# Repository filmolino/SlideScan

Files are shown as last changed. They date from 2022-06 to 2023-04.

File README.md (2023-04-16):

# SlideScan

**Note:** There is a new version of the slide scanner using a M5Stack Fire for more info visit [Filmolino SlideScanner](https://github.com/filmolino/SlideScanner)

Filmolino SlideScan is a device that makes it easy to scan slides in magazines fully automatic using a modified slide projector and a digital camera. It controls the slide projector and a digital camera using a cable release or an infrared remote control (Nikon, Canon, Pentax, Sony, Olympus, Minolta). It is powered directly from the slide projector or over a mini USB connector. New cable releases and IR controls can easy be added to the software. 
 
Thanks to the [M5StampC3 from M5Stack](https://shop.m5stack.com/collections/m5-controllers/products/m5stamp-c3-mate-with-pin-headers) using a [ESP32-C3 RISC-V microcontroller from Espressif](https://www.espressif.com/en/products/socs/esp32-c3) it is also possible to control the SlideScan through a web interface over WiFi. The scanner has it's own access point to which you can connect.

Everything of the SlideScan is open source, so you can easy build your own!

## Guide
### Camera connection
You can connect your digital camera using a cable connection or infrared remote control. To control your camera using the cable release you need a shutter release cable for your camera with a 2.5 mm jack connector on the other end. You can find the right cable for your camera searching the web for *JJC Remote Control Shutter Release Cable*. They are not expensive you should get one for about 10 EUR.

### DIN cable connection to pcb
Connect the male 6 pin DIN connector as follows to the PCB J2:

| Pin DIN | Pin PCB |Function |
| --- | --- | --- |
| 1 | 4 | Reverse slide transport |
| 2 | 3 | Forward slide transport |
| 3 | 2 | Positive DC voltage |
| 4 | x | Not used |
| 5 | x | Not used |
| 6 | 1 | Negative DC voltage (only needed if you want to power SlideScan from the projector) |

### Slide projector connection
**Important: Use the Tape/remote control socket and not the lap dissolve socket.**
Connect the 6 pin DIN connector of the Filmolino SlideScan to the *remote control socket* of your slide projector. SlideScan can be powered from the slide projector or you can power it over the Mini USB connector. 

To power it from the projector the following components *R2, C4, U1, C3, D2* need to be assembled on the pcb. If you power SlideScan over USB you don't need this components.

To not damage your SlideScan or slide projector check the pin map below first!
| 6 pin DIN connector | Function |
| --- | --- |
| 1 | Reverse slide transport |
| 2 | Forward slide transport |
| 3 | Positive DC voltage **max. 42 VDC!** (This voltage is usually about 30...35 VDC on most slide projectors) |
| 4 | Focus motor |
| 5 | Not used |
| 6 | Negative DC voltage |

### USB power
If you don't want to power your SlideScan from the slide projector connect an USB charger to the mini USB connector of the SlideScan.

### Turn on
Now you are ready to turn SlideScan on. To do so turn on the slide projector and if needed the USB charger.
After turning on the green LED should light up and the red one slowly blinking (because there is no WiFi connection yet).

### WiFi Connection
SlideScan starts its own WiFi access point: 

Default WiFi credentials
| ID | value |
| --- | --- |
| SSID | scanner |
| Password | filmolino |
| IP | 192.168.4.1 |

To see the web user interface do the following:
1. Connect your PC/Tablet/... to the SlideScan network with the SSID **scanner** using the password **filmolino**
2. In your webbrowser enter the address: **192.168.4.1**
3. Now you should see the web interface of the scanner

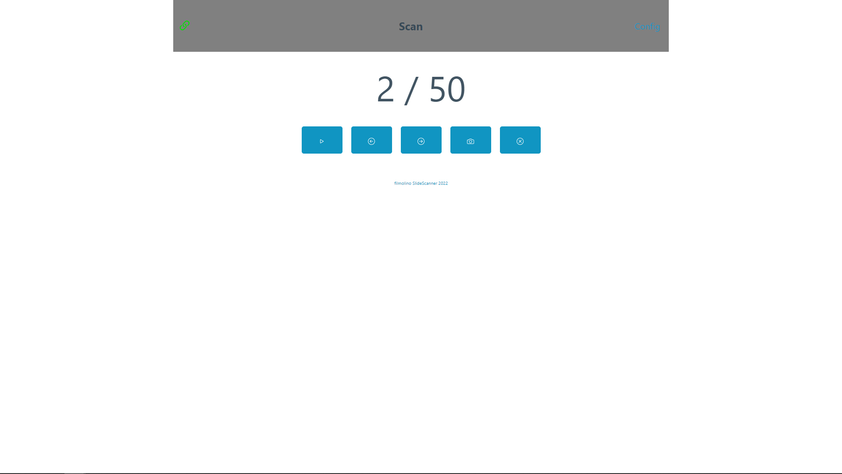
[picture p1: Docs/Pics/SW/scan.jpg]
Scanner Web interface scan dialog


### Configuration
To see the configuration menu click on **Config**.

#### Access Point
Here you can change the SSID and the password.

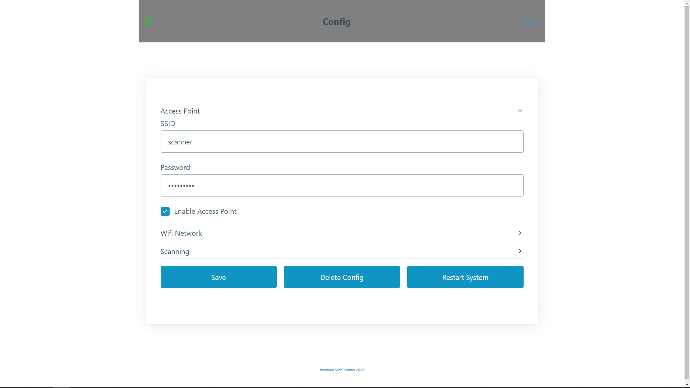
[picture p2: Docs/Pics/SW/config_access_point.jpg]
Config access point


#### WiFi Network
Not implemented yet.

#### Scanning
Here you can config the SlideScan.

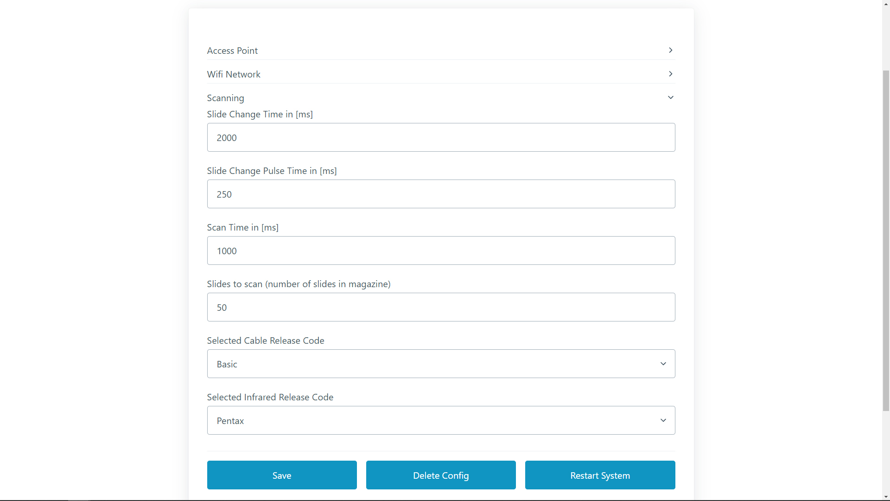
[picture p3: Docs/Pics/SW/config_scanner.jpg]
Config scanner


##### Slide Change Time
This is the time the slide projector needs to change the slide.
Unit is milliseconds (1 second = 1000 milliseconds)

##### Slide Change Pulse Time
Duration of the pulse for the slide transport. During this time the slide transport contacts are closed. 
Unit is milliseconds (1 second = 1000 milliseconds)

##### Scan Time
This is the time the digital camera needs to capture (scan) the slide
Unit is milliseconds (1 second = 1000 milliseconds)

##### Slides to scan
Number of slides in the magazine.

##### Selected cable release
Can be OFF or the cable release you want to use.

##### Selected Infrared Release Code
Can be OFF or the brand name of your digital camera.

##### Buttons
| Button | Function |
| --- | --- |
| Save | Saves the changes |
| Delete Config | Deletes the actual configuration, you need to click the *Restart System* button after that |
| Restart System | Restarts the scanner |

### Standalone operation 
The device is controlled with only two buttons. The functions are as follows:

| Button | Short press | Long press |
| --- | --- | --- |
| Left | Forward slide transport | Backward slide transport |
| Right | Trigger camera (if auto an auto scan is active, stop it) | Start auto scan |

The actual state is indicated by a bi-color LED:
| State | LED green | LED red |
| --- | --- | --- |
| Running and no WiFi connection | ON | BLINK slowly |
| Running with WiFi connection | ON | OFF |
| Auto scan active | BLINK | OFF |
| Error | OFF | ON |

#### Auto Scan
When starting an Auto Scan the scan is always starts with image 1 and then the number of images is scanned. If the image counter is higher it will be reset to 1 before start.

### WiFi operation
Connect to the WiFi and open the address **192.168.4.1** in your webbrowser as described above. The SlideScan is connected as long as you see the green connected sign in the top left corner.

This view shows the current slide counter and the slides in the magazine (0/50). 
You can start an auto scan or manually scan slides using the five buttons below. If you want to change the current configuration click *Config* in the top right corner.

Buttons
| Button 1 | Button 2 | Button 3 | Button 4 | Button 5 |
| --- | --- | --- | --- | --- |
| Start Auto Scan | Forward | Backward | Capture (Scan) | Reset current slide |

To change to number of slides in the current magazine you can click on the current slide counter or go to the config menu.

## Hardware
You can find the KiCAD project with complete schematic and pcb design in the hardware folder. The double sided pcb can be easily soldered by hand. It uses just a few SMD components in not too small cases (0805). The components are easily available from the usual distributors.

## Software
### Project
The software is build with ESP-IDF using platform.io and Visual Studio Code.

## Documentation
The documentation with images can be found in the docs folder.

## To do
- slidescan.local address not working yet. So you have to point your browser to the default IP **192.168.4.1**
- Station mode (to connect to a WiFi network) not working yet
- Tested with Nikon and Pentax cameras

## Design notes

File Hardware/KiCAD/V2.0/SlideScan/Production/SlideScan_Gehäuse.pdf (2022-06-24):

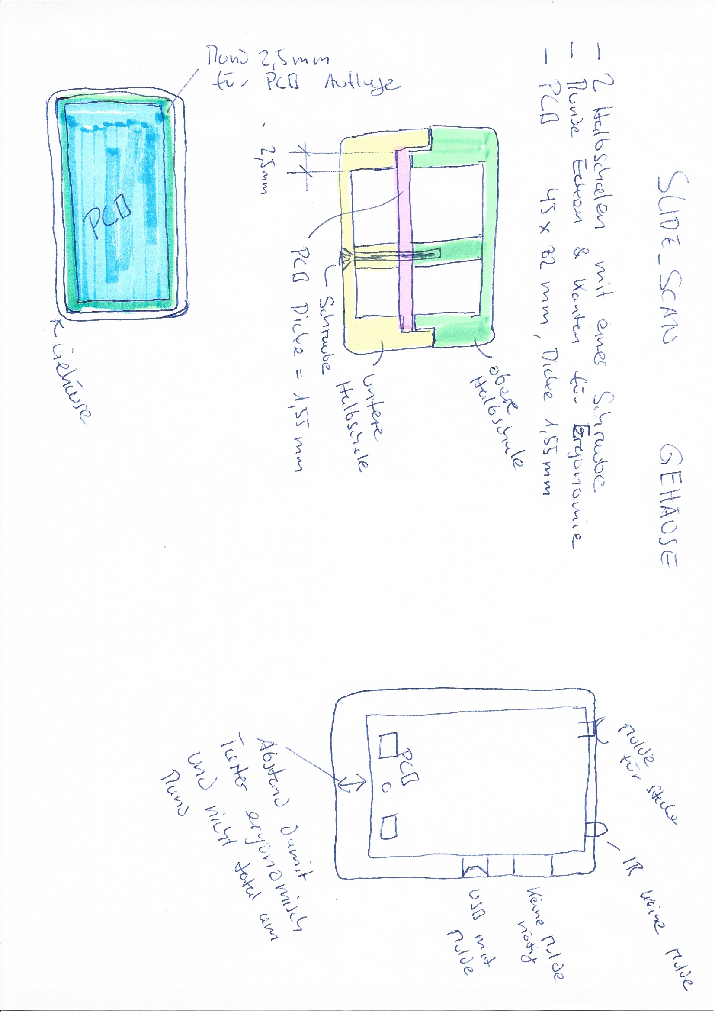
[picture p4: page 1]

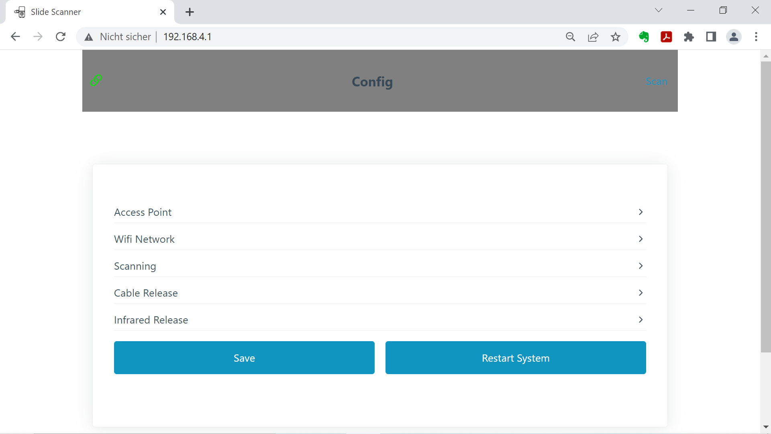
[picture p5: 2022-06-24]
Docs/Pics/Prototype/Screenshot (2).png

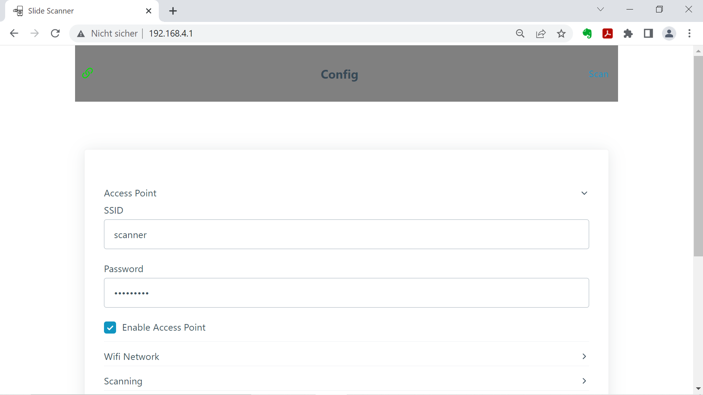
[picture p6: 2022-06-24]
Docs/Pics/Prototype/Screenshot (4).png

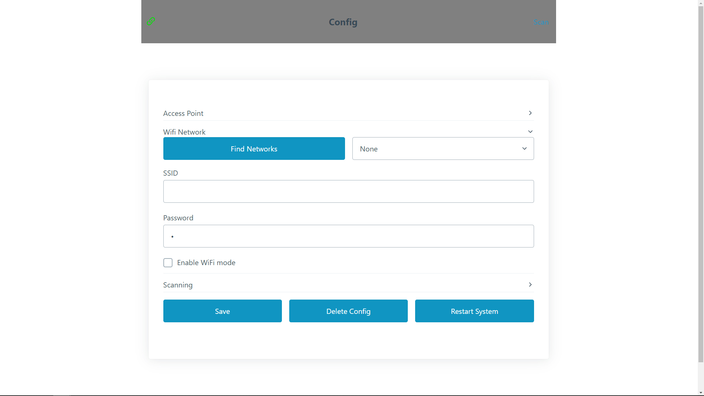
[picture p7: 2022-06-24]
Docs/Pics/SW/config_wifi.jpg

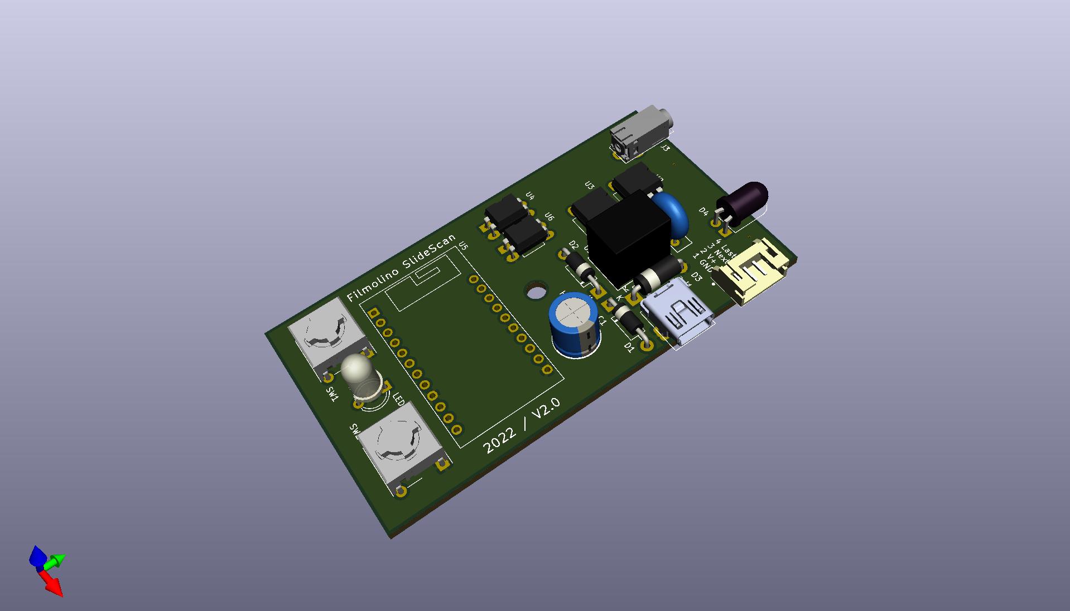
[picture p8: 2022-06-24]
Docs/Pics/HW/V2.0/SlideScan_TopView_KiCAD.jpg

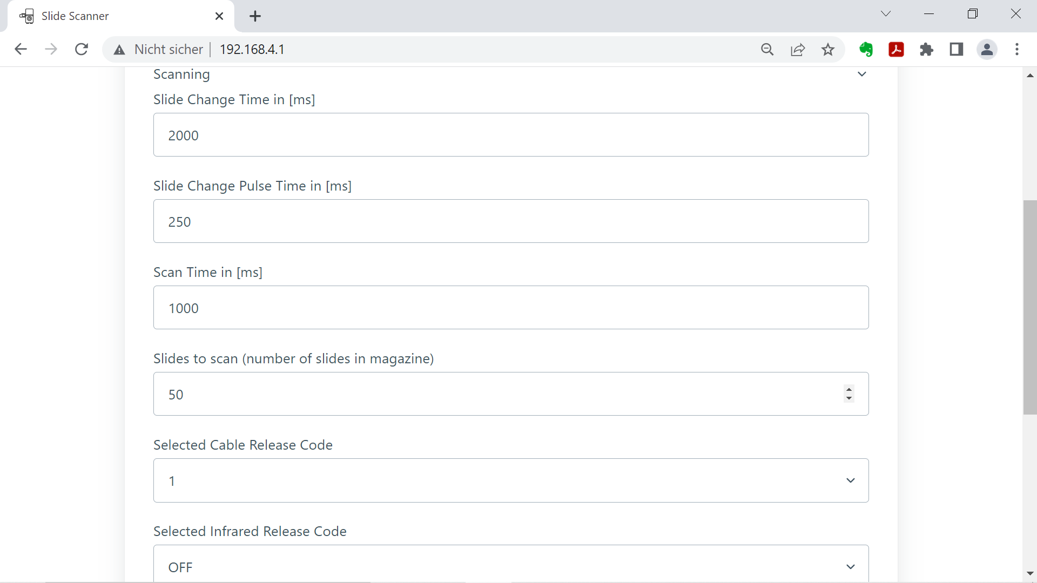
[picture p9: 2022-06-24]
Docs/Pics/Prototype/Screenshot (3).png

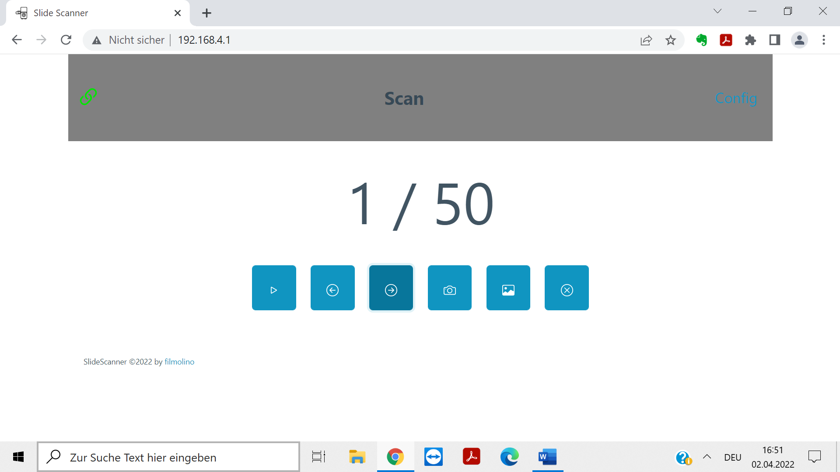
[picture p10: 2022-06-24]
Docs/Pics/Prototype/Screenshot (1).png

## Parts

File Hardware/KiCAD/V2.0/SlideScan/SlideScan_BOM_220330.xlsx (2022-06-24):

Ref | Qnty | Value | Cmp name | Footprint | Lieferant | Einzelpreis [EUR] | Preis [EUR]
C1, | 1 | 470uF/10V | CP | Capacitor_THT:CP_Radial_D8.0mm_P3.50mm | Reichelt | 0.4 | 0.4
C2, C5, | 2 | 100nF/50V/MLCC | C | Capacitor_SMD:C_0805_2012Metric_Pad1.15x1.40mm_HandSolder | Reichelt | 0.1 | 0.2
C3, C6, | 2 | 10uF/10V/MLCC | C | Capacitor_SMD:C_0805_2012Metric_Pad1.15x1.40mm_HandSolder | Distrelec | 0.4 | 0.8
C4, | 1 | 10uF/100V/MLCC | C | Capacitor_SMD:C_1210_3225Metric_Pad1.42x2.65mm_HandSolder | Distrelec | 0.7 | 0.7
D1, D2, | 2 | 1N5817 | 1N5817 | Diode_THT:D_DO-41_SOD81_P10.16mm_Horizontal | Reichelt | 0.1 | 0.2
D3, | 1 | BZW06-5V8 | 1N62xxA | Diode_THT:D_DO-15_P10.16mm_Horizontal | Reichelt | 0.3 | 0.3
D4, | 1 | LD 274 | LED | LED_THT:LED_D5.0mm_Horizontal_O1.27mm_Z3.0mm_IRBlack | Reichelt | 1.1 | 1.1
F1, | 1 | FRX03060F | Polyfuse | Varistor:RV_Disc_D9mm_W3.3mm_P5mm | Reichelt | 0.4 | 0.4
J1, | 1 | USB_B_Mini RND 205-00862 | USB_B_Mini | SlideScan:USB_Mini_RND_205-00862 | Distrelec | 1.35 | 1.35
J2, | 1 | Conn_01x04 | Conn_01x04 | Connector_PinSocket_2.54mm:PinSocket_1x04_P2.54mm_Vertical | Einlöten | 0 | 0
J3, | 1 | Lumberg 1501 04 | AudioJack3 | SlideScan:Jack_2.5mm_Lumberg_1501_04 | Reichelt | 1.2 | 1.2
L1, | 1 | L | L | Inductor_SMD:L_0805_2012Metric_Pad1.15x1.40mm_HandSolder | Reichelt | 0.3 | 0.3
LED1, | 1 | Everlight 339-1SDRSYGW/S530-A3/S150 | LED_Dual_ACA | SlideScan:LED_D5.0mm-3_Everlight | Reichelt | 0.2 | 0.2
Q1, | 1 | BSS138 | BSS138 | Package_TO_SOT_SMD:SOT-23 | Reichelt | 0.2 | 0.2
R1, R2, R3, R4, R8, R9, R10, | 7 | 180R | R | Resistor_SMD:R_0805_2012Metric_Pad1.15x1.40mm_HandSolder | Reichelt | 0.05 | 0.35
R5, | 1 | R | R | Resistor_SMD:R_0805_2012Metric_Pad1.15x1.40mm_HandSolder | Reichelt | 0.05 | 0.05
R6, | 1 | 10k | R | Resistor_SMD:R_0805_2012Metric_Pad1.15x1.40mm_HandSolder | Reichelt | 0.05 | 0.05
R7, | 1 | 1M | R | Resistor_SMD:R_0805_2012Metric_Pad1.15x1.40mm_HandSolder | Reichelt | 0.05 | 0.05
R11, | 1 | 0R | R | Resistor_SMD:R_0805_2012Metric_Pad1.15x1.40mm_HandSolder | Reichelt | 0.05 | 0.05
SW1, SW2, | 2 | MEC APEM 5ETH935 | SW_Push | SlideScan:SW_MEC_5ETH9 | Reichelt | 1.35 | 2.7
U1, | 1 | R78C5.0-1.0 | R78C5.0-1.0 | SlideScan:RECOM_SIP3_R-78C5.0-1.0 | Reichelt | 11.5 | 11.5
U2, U3, U4, U6, | 4 | VO14642AT | VO14642AT | Package_DIP:DIP-6_W7.62mm | Distrelec | 3.2 | 12.8
U5, | 1 | M5StampC3_C3U | M5StampC3_C3U | SlideScan:M5StampC3 | Distrelec | 7.1 | 7.1 | C3U Version
Gehäuse | 1 | Hammond MFG 1591XXABK |  |  | Reichelt | 3.75 | 3.75
Tasterkappen | 2 | Apem MEC 12 mm 1SS09-12.0 |  |  | Reichelt | 0.25 | 0.5
PCB | 1 | PCB |  |  | MultiCircuitBoards | 7.5 | 7.5
 |  |  |  |  |  | TOTAL | 53.75
 |  |  |  |  |  | Ohne PCB | 46.25
 |  |  |  |  |  | Ohne Dia Power | 41.15

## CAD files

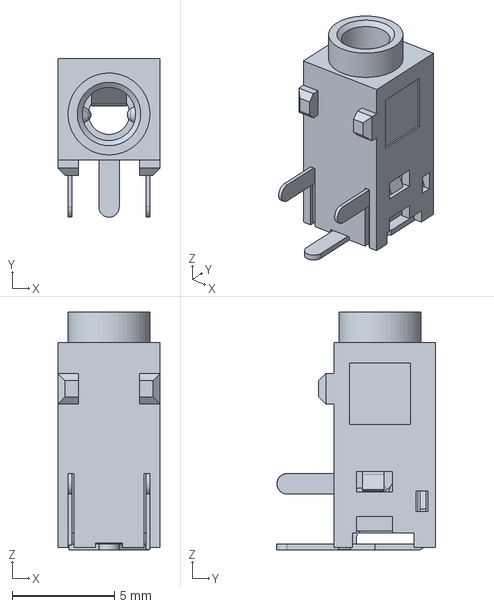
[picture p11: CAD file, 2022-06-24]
Hardware/Footprints/3d/lumberg_1501_04.stp
5.00 x 7.75 x 11.6 mm

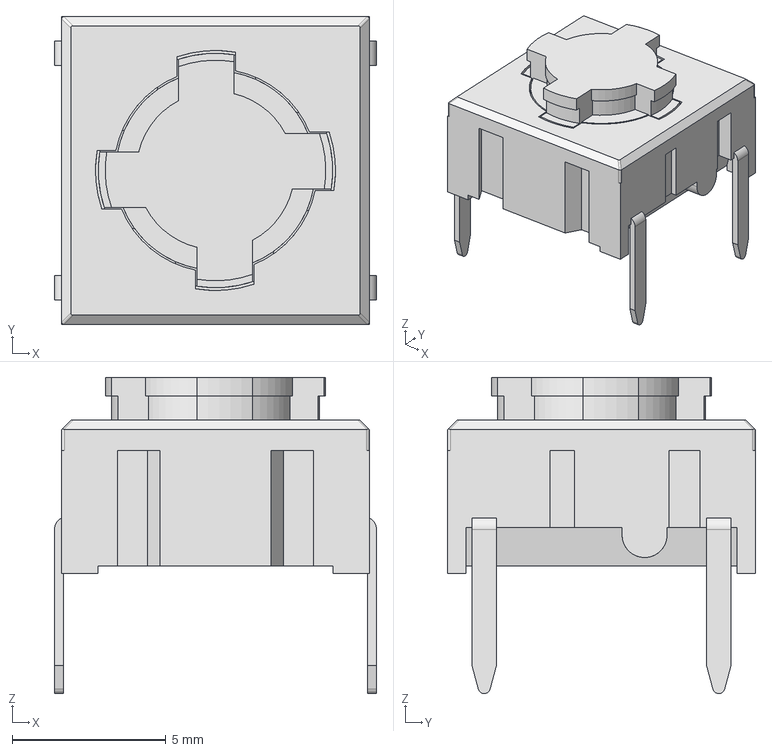
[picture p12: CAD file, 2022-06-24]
Hardware/Footprints/3d/5ETH9XX.stp
10.5 x 10.0 x 10.3 mm

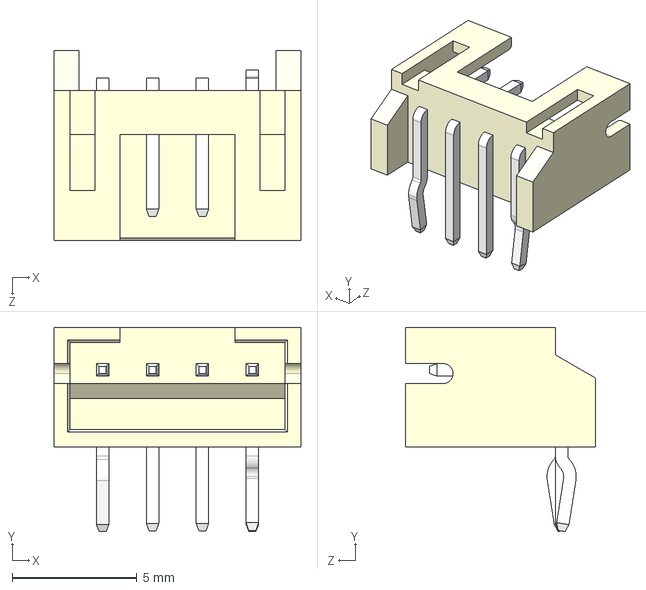
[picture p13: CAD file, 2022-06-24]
Hardware/Footprints/3d/S4B-PH-K-S(LF)(SN)--3DModel-STEP-56544.STEP
9.90 x 8.18 x 7.60 mm

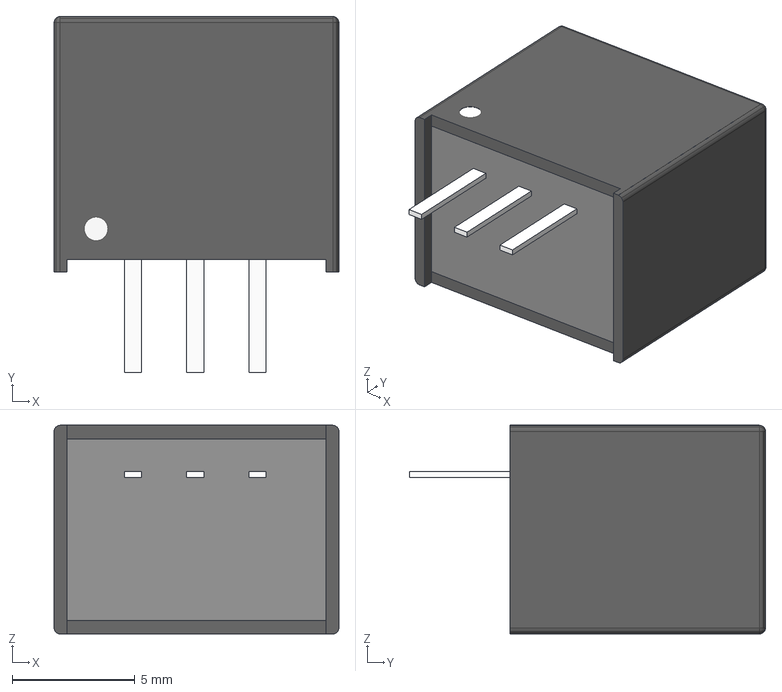
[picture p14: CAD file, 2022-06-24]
Hardware/Footprints/3d/R-78C5.0-1.0--3DModel-STEP-1.STEP
11.6 x 14.5 x 8.51 mm

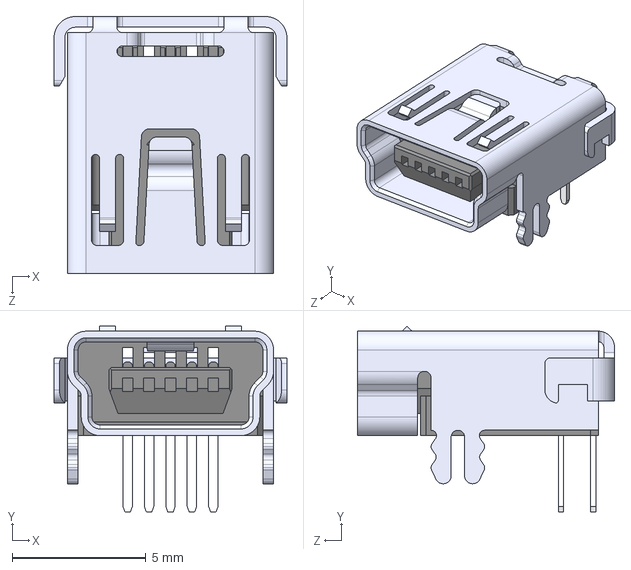
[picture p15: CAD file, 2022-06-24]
Hardware/Footprints/3d/2172034-1--3DModel-STEP-56544.STEP
8.70 x 6.94 x 9.60 mm

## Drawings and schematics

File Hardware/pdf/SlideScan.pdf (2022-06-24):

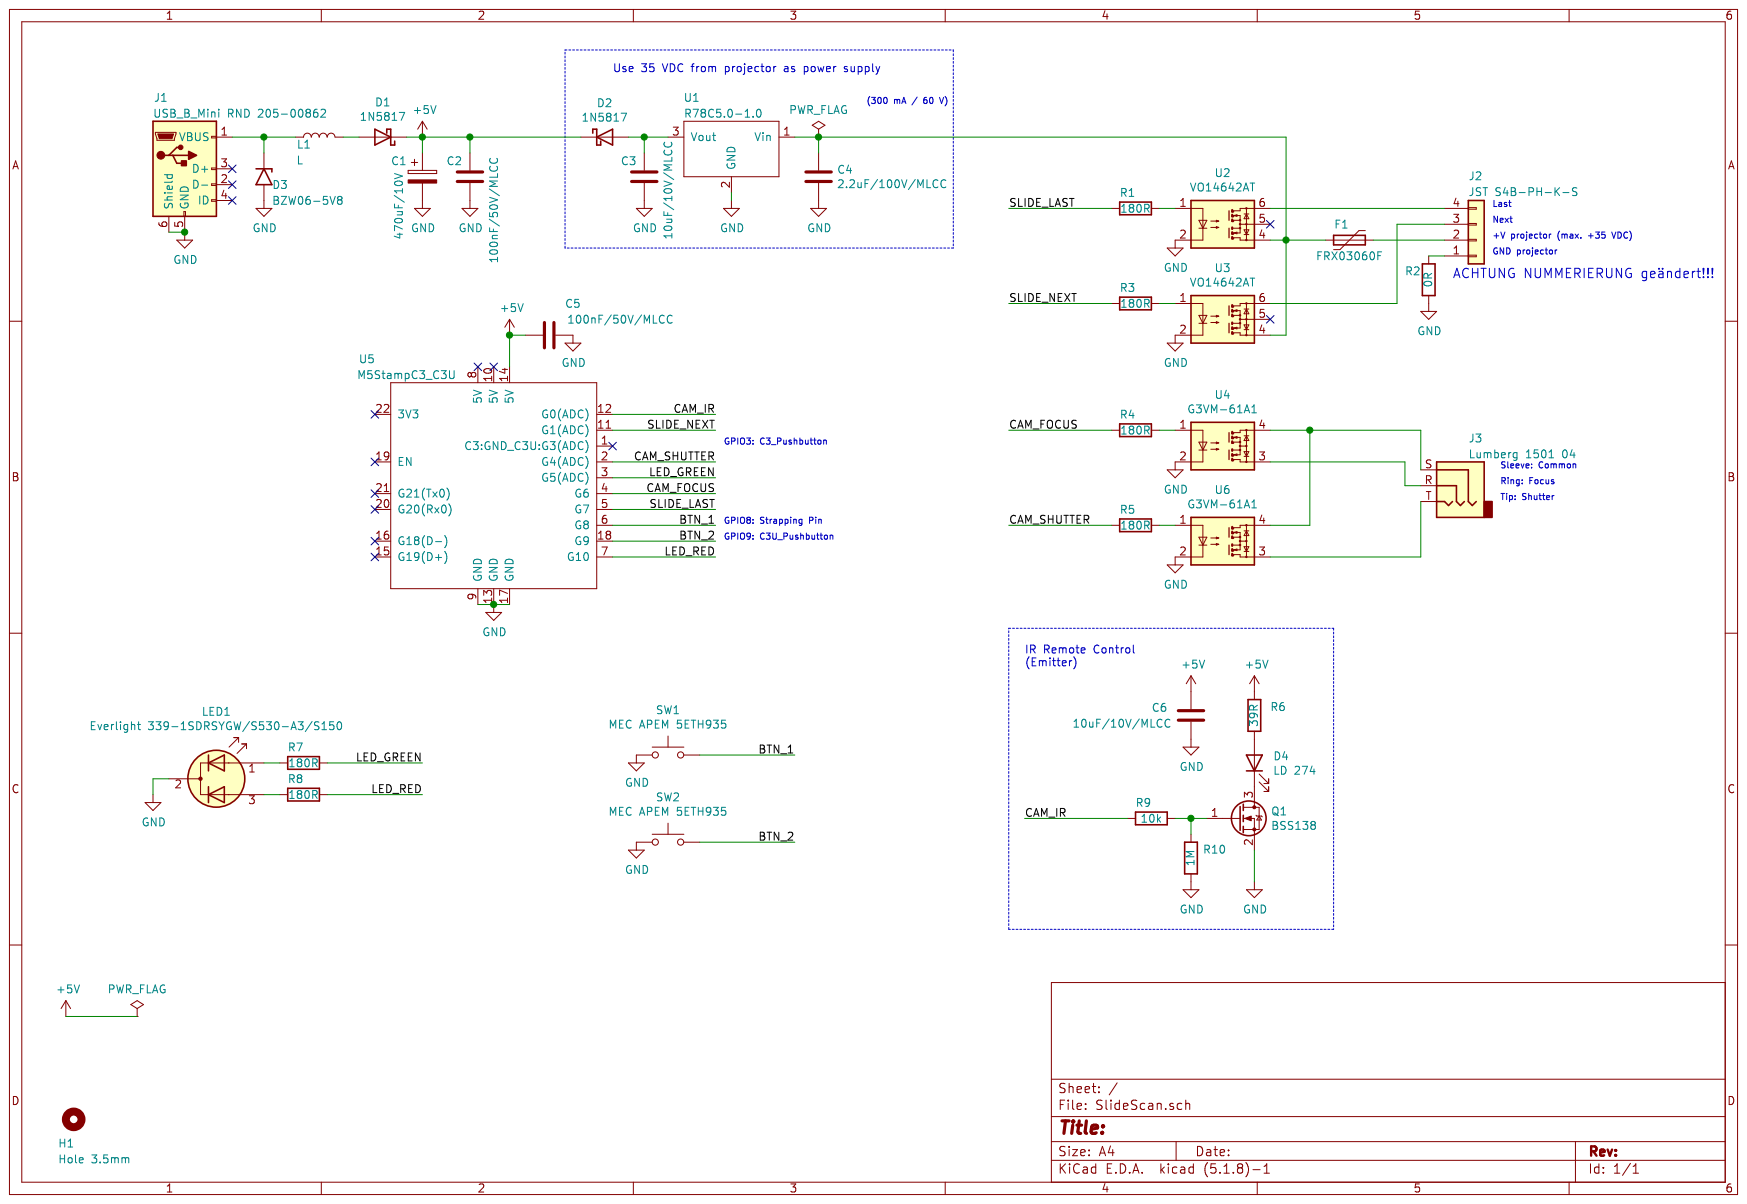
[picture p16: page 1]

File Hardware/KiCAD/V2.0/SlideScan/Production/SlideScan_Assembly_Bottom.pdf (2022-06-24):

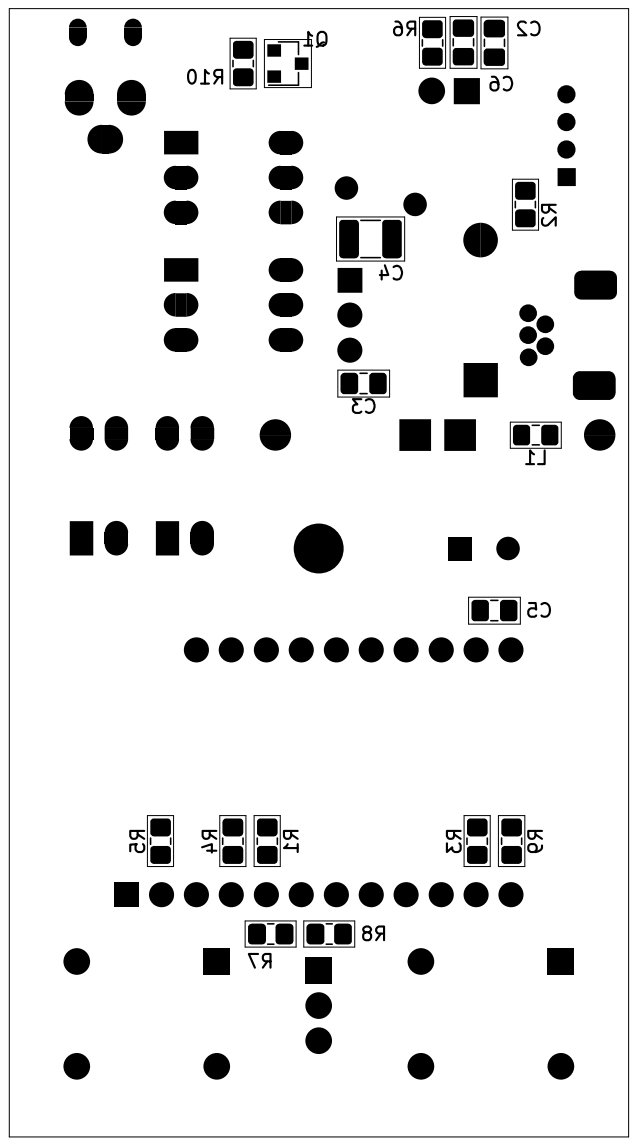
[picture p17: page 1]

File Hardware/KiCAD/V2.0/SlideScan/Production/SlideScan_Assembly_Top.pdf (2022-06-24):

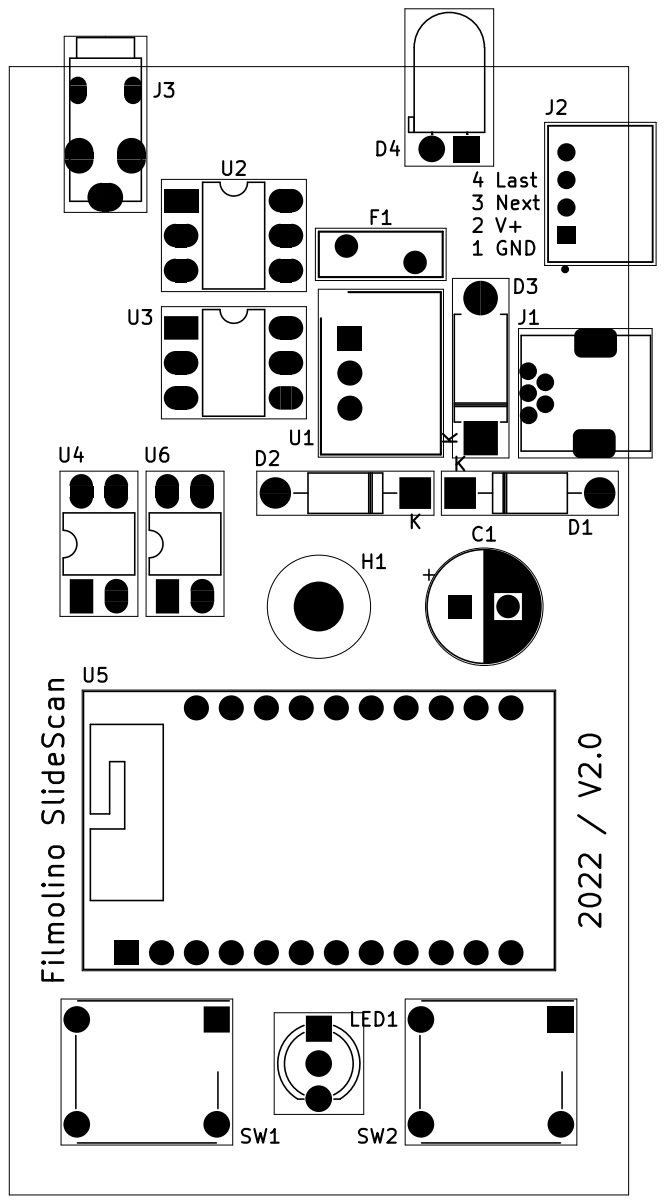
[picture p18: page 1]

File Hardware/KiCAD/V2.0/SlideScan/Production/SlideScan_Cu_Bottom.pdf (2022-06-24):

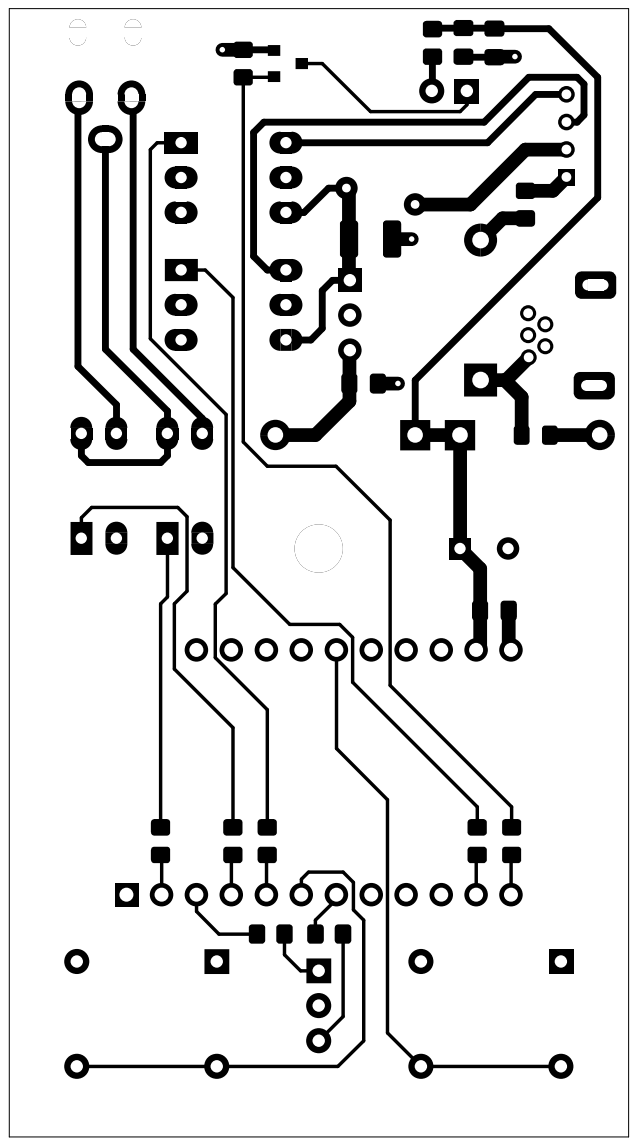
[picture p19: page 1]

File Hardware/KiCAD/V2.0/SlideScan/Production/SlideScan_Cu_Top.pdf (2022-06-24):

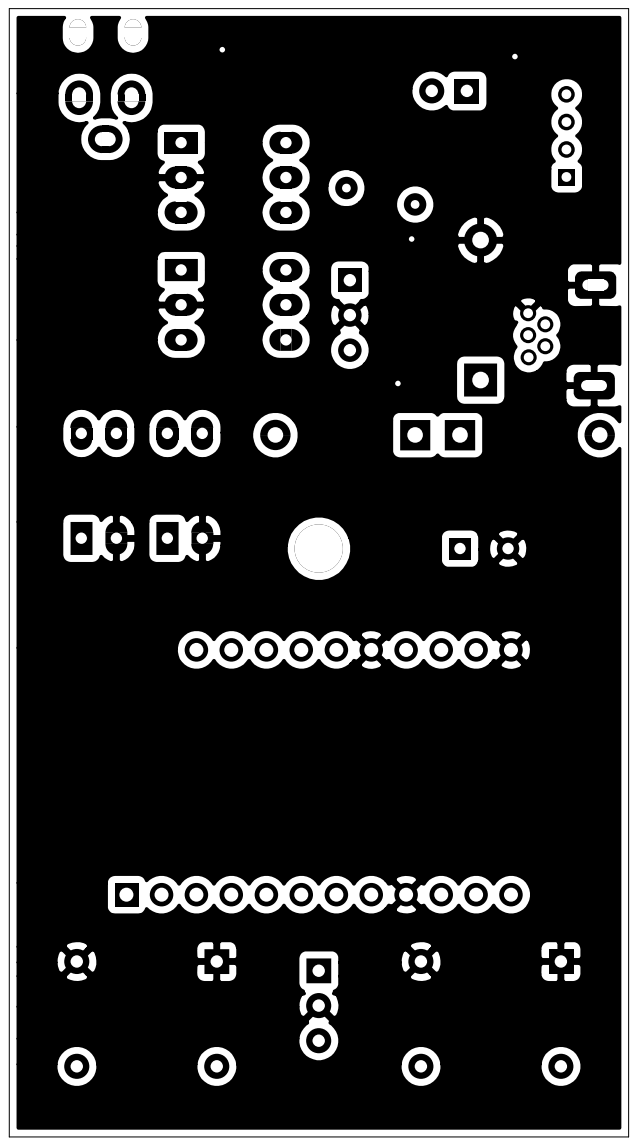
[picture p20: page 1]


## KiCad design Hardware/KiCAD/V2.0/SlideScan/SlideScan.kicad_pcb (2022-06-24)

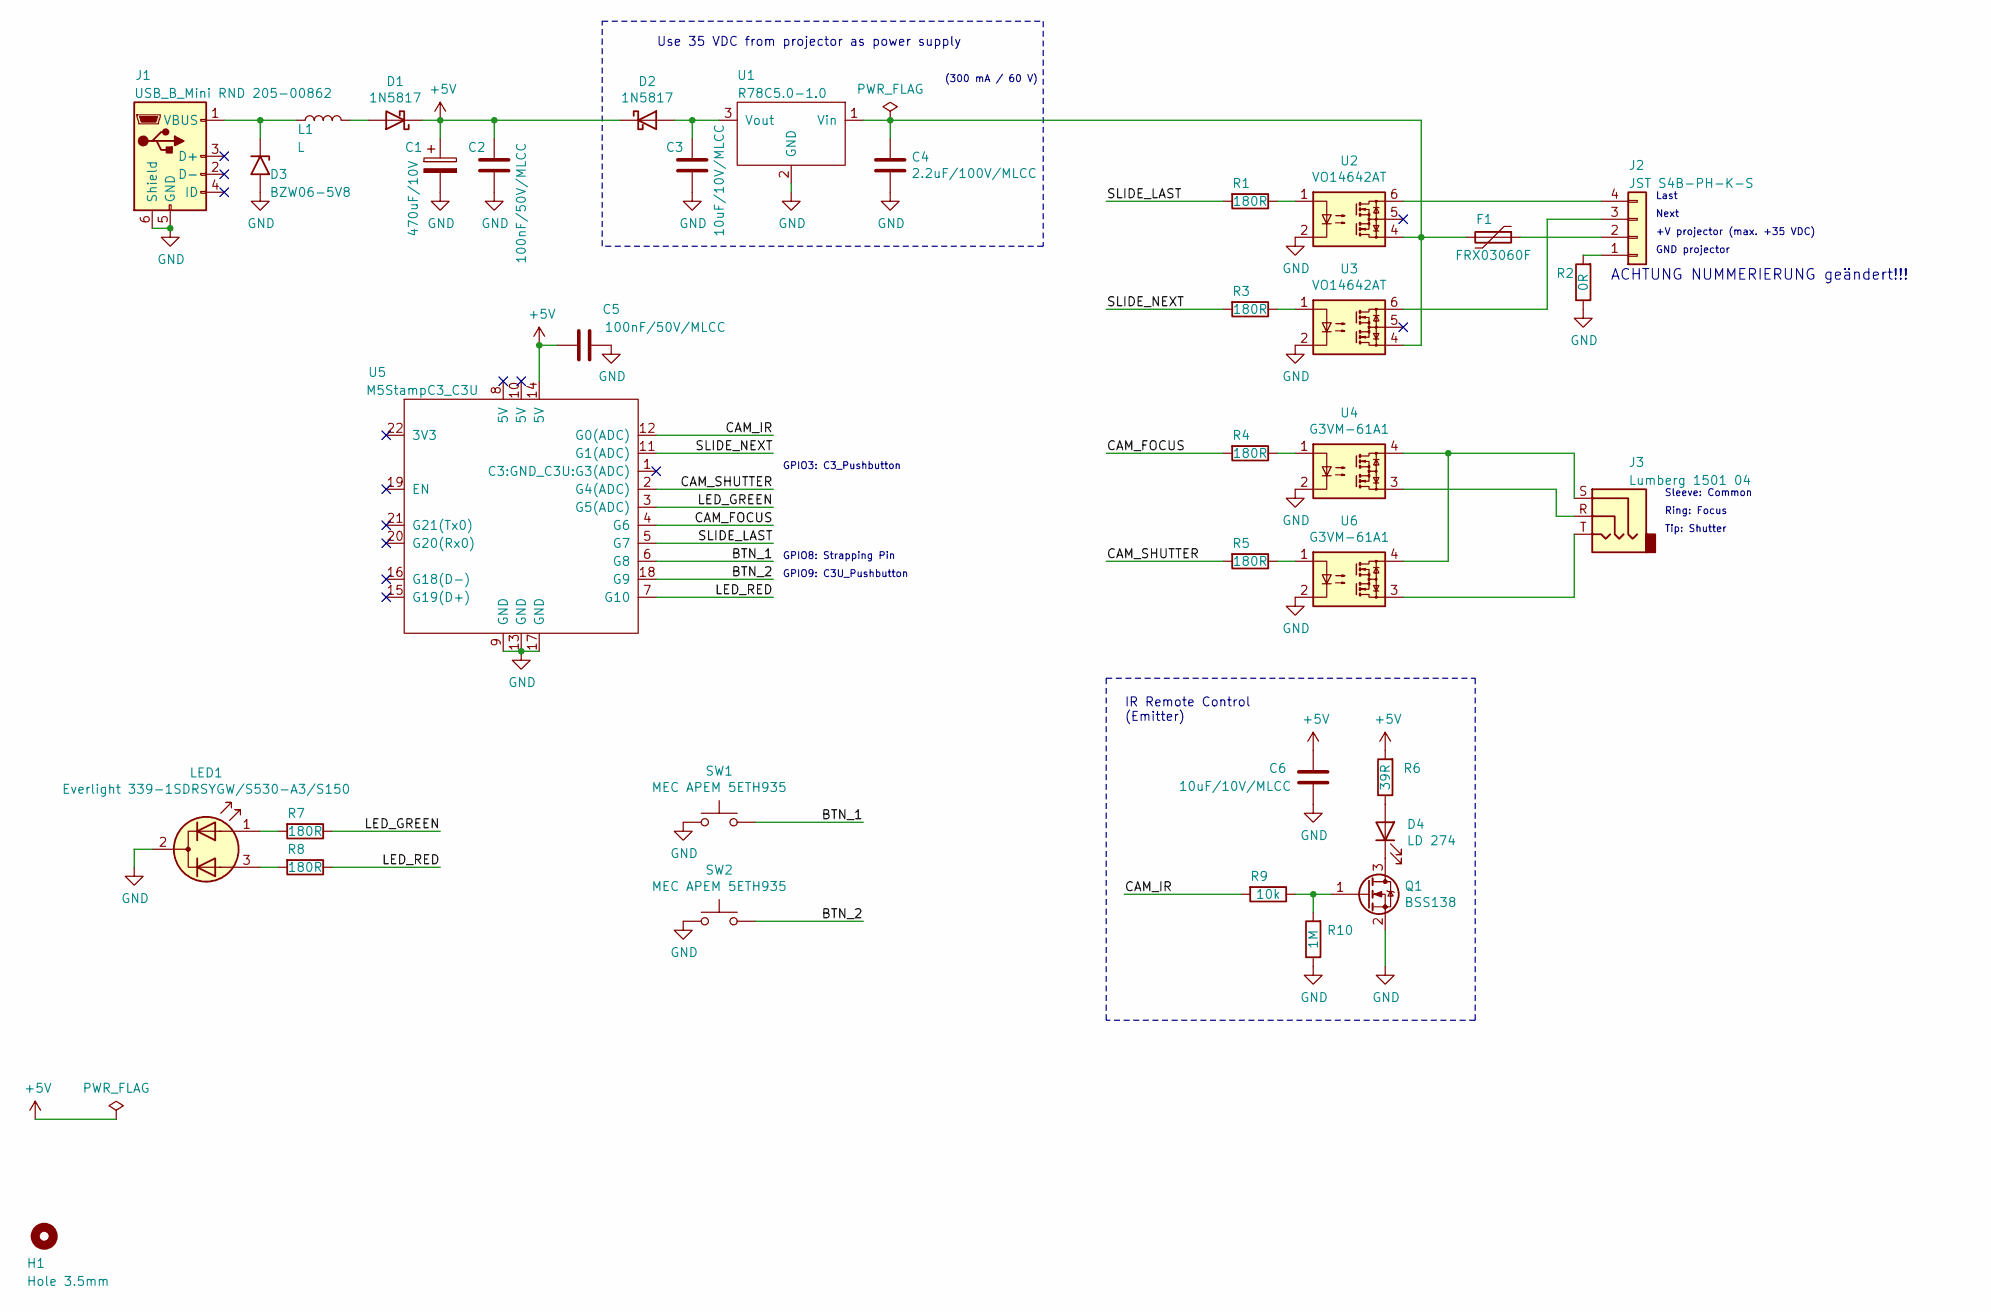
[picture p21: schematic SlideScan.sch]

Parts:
C1: 470uF/10V; CP_Radial_D8.0mm_P3.50mm
C2, C5: 100nF/50V/MLCC; C_0805_2012Metric_Pad1.18x1.45mm_HandSolder
C3, C6: 10uF/10V/MLCC; C_0805_2012Metric_Pad1.18x1.45mm_HandSolder
C4: 2.2uF/100V/MLCC; C_1210_3225Metric_Pad1.33x2.70mm_HandSolder
D1, D2: 1N5817; D_DO-41_SOD81_P10.16mm_Horizontal
D3: BZW06-5V8; D_DO-15_P10.16mm_Horizontal
D4: LD 274; LED_D5.0mm_Horizontal_O1.27mm_Z3.0mm_IRBlack
F1: FRX03060F; RV_Disc_D9mm_W3.3mm_P5mm
H1: Hole 3.5mm; MountingHole_3.5mm
J1: USB_B_Mini RND 205-00862; USB_Mini_RND_205-00862
J2: JST S4B-PH-K-S; JST_S4B-PH-K-S(LF)(SN)
J3: Lumberg 1501 04; Jack_2.5mm_Lumberg_1501_04
L1: L; L_0805_2012Metric_Pad1.15x1.40mm_HandSolder
LED1: Everlight 339-1SDRSYGW/S530-A3/S150; LED_D5.0mm-3_Everlight
Q1: BSS138; SOT-23
R1, R3, R4, R5, R7, R8: 180R; R_0805_2012Metric_Pad1.20x1.40mm_HandSolder
R2: 0R; R_0805_2012Metric_Pad1.20x1.40mm_HandSolder
R6: 39R; R_0805_2012Metric_Pad1.20x1.40mm_HandSolder
R9: 10k; R_0805_2012Metric_Pad1.20x1.40mm_HandSolder
R10: 1M; R_0805_2012Metric_Pad1.20x1.40mm_HandSolder
SW1, SW2: MEC APEM 5ETH935; SW_MEC_5ETH9
U1: R78C5.0-1.0; RECOM_SIP3_R-78C5.0-1.0
U2, U3: VO14642AT; DIP-6_W7.62mm_LongPads
U4, U6: G3VM-61A1; DIP-4_W7.62mm_LongPads
U5: M5StampC3_C3U; M5StampC3

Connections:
+5V: C1.1, C2.1, C5.2, C6.1, D1.1 (K), D2.1 (K), R6.2, U5.14 (5V)
/BTN_1: SW1.2, U5.6 (G8)
/BTN_2: SW2.2, U5.18 (G9)
/CAM_FOCUS: R4.2, U5.4 (G6)
/CAM_IR: R9.2, U5.12 (G0(ADC))
/CAM_SHUTTER: R5.2, U5.2 (G4(ADC))
/LED_GREEN: R7.1, U5.3 (G5(ADC))
/LED_RED: R8.1, U5.7 (G10)
/SLIDE_LAST: R1.2, U5.5 (G7)
/SLIDE_NEXT: R3.2, U5.11 (G1(ADC))
GND: C1.2, C2.2, C3.2, C4.2, C5.1, C6.2, D3.2 (A2), J1.5 (GND), J1.6 (Shield), LED1.2 (K), Q1.2 (S), R2.1, R10.1, SW1.1, SW2.1, U1.2 (GND), U2.2, U3.2, U4.2, U5.9 (GND), U5.13 (GND), U5.17 (GND), U6.2
unnamed: C3.1, D2.2 (A), U1.3 (Vout)
unnamed: C4.1, F1.2, U1.1 (Vin), U2.4, U3.4
unnamed: D1.2 (A), L1.2
unnamed: D3.1 (A1), J1.1 (VBUS), L1.1
unnamed: D4.1 (K), Q1.3 (D)
unnamed: D4.2 (A), R6.1
unnamed: F1.1, J2.2
unnamed: J2.1, R2.2
unnamed: J2.3, U3.6
unnamed: J2.4, U2.6
unnamed: J3.R, U4.3
unnamed: J3.S, U4.4, U6.4
unnamed: J3.T, U6.3
unnamed: LED1.1 (A1), R7.2
unnamed: LED1.3 (A2), R8.2
unnamed: Q1.1 (G), R9.1, R10.2
unnamed: R1.1, U2.1
unnamed: R3.1, U3.1
unnamed: R4.1, U4.1
unnamed: R5.1, U6.1

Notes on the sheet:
Use 35 VDC from projector as power supply
GPIO3: C3_Pushbutton
GPIO9: C3U_Pushbutton
(300 mA / 60 V)
Last
Next
+V projector (max. +35 VDC)
GND projector
Sleeve: Common
Ring: Focus
Tip: Shutter
IR Remote Control (Emitter)
GPIO8: Strapping Pin
ACHTUNG NUMMERIERUNG geändert!!!

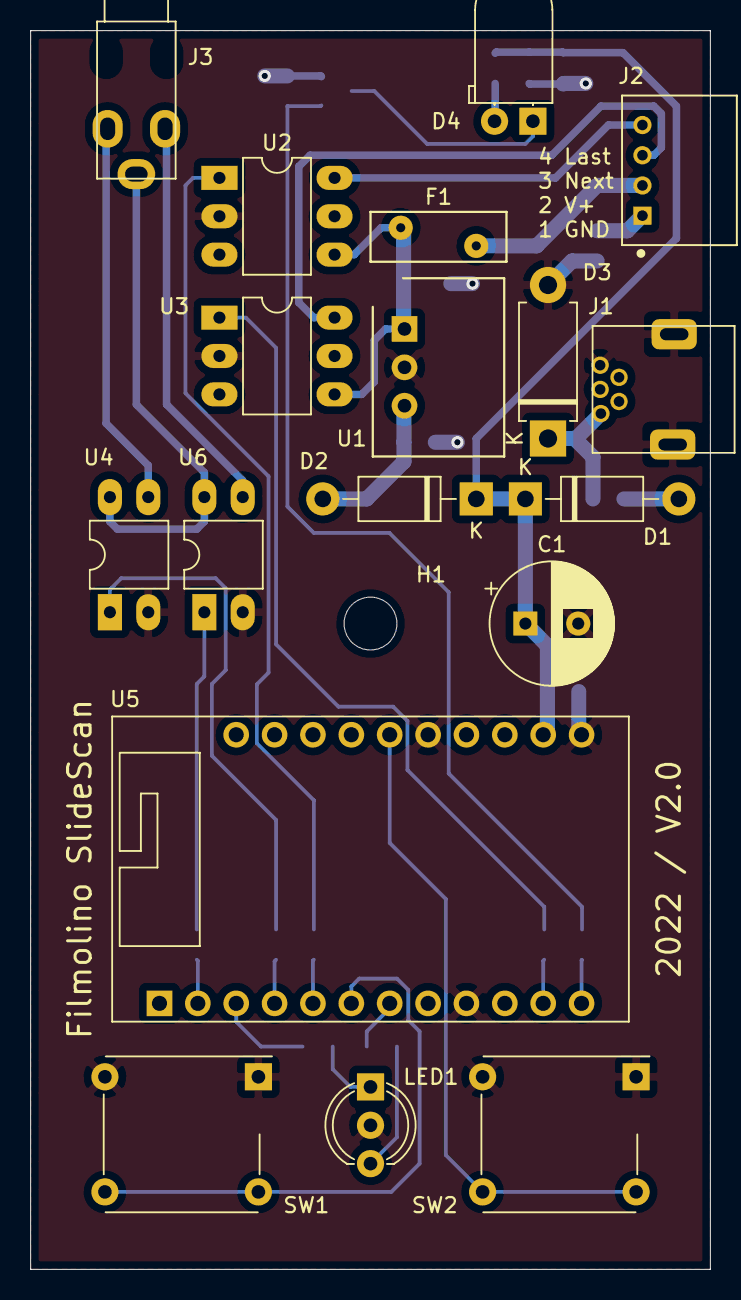
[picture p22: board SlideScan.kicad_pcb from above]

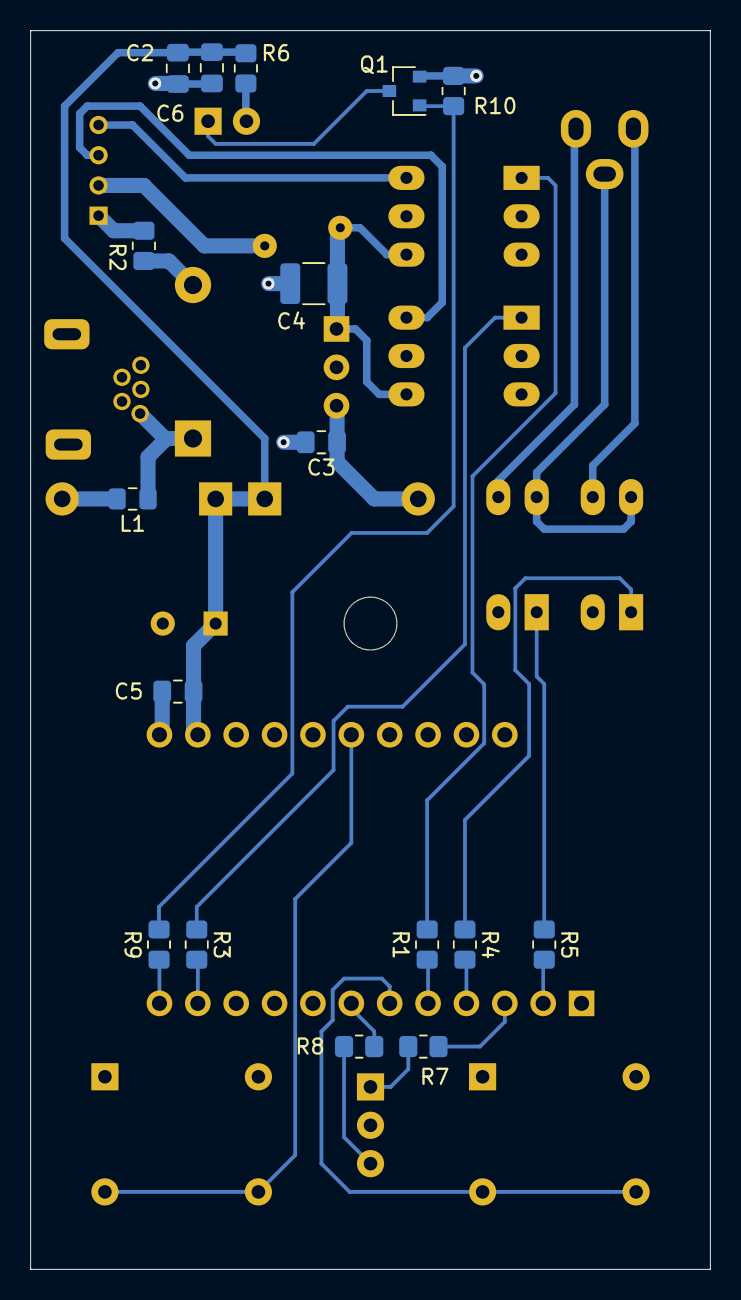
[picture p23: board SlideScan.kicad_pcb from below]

Board: 2 copper layers, 45.0 x 82.0 mm, 36 parts (17 on the bottom side), 31 nets.

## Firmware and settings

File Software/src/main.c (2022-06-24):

#include <stdio.h>
#include <string.h>
#include <sys/unistd.h>
#include <sys/stat.h>
#include "project.h"
#include "esp_err.h"
#include "esp_log.h"
#include "esp_spiffs.h"
#include "esp_wifi.h"
#include "nvs_flash.h"
#include "freertos/FreeRTOS.h"
#include "freertos/task.h"
#include "freertos/queue.h"
#include "driver/gpio.h"
#include "driver/rmt.h"
#include "config.h"
#include "control.h"
#include "cable_release.h"
#include "ir_release.h"
#include "wifi.h"
#include "server.h"

// LOG TAG
static const char *TAG = "app_main";

// Queues
static QueueHandle_t control_evt_queue = NULL;

// TASK: BUTTON 
void task_button(void *param) {
  static bool btnPressed[3] = { false, false, false };
  static TickType_t btnPressedTime[3] = { 0, 0 , 0 };
  gpio_num_t gpio = GPIO_BTN1;
  control_evt_t evt;

  while (1) {
    for (uint32_t n = 0; n < 3; n++) {
      if      (n == 0) { gpio = GPIO_BTN1; }
      else if (n == 1) { gpio = GPIO_BTN2; }
      else if (n == 2) { gpio = GPIO_INTERNAL_BUTTON; }
  
      if (gpio_get_level(gpio) == 0) {
        // Button is pressed
        if (!btnPressed[n]) {
          btnPressedTime[n] = 0;
          btnPressed[n] = true;
          ESP_LOGI(TAG, "button pressed[%d]", n);
        }
        else {
          btnPressedTime[n]++;
        }
      }
      else {
        // Button is not pressed
        if (btnPressed[n]) {
          // Button released => set Event
          btnPressed[n] = false;
          if (n == 0) { 
            evt = btnPressedTime[n] < BTN_SHORT_PRESS_TIME_MAX ? CONTROL_EVT_NEXT : CONTROL_EVT_LAST; 
          }
          if (n == 1) { 
            if (btnPressedTime[n] < BTN_SHORT_PRESS_TIME_MAX) {
              if (control_is_scanning()) {
                evt = CONTROL_EVT_STOP;
              } else {
                evt = CONTROL_EVT_SCAN;
              }
            } else { 
              control_reset_current_slide();    // Set current_slide to 0, so the scan starts with Image1
              evt = CONTROL_EVT_START; 
            }
          }
          if (n == 2) { 
            evt = btnPressedTime[n] < BTN_SHORT_PRESS_TIME_MAX ? CONTROL_EVT_BTN_INTERNAL_SHORT : CONTROL_EVT_BTN_INTERNAL_LONG; 
            wifi_scan_start();
          }
          ESP_LOGI(TAG, "button[%d] released, pressedTime=%d", n, btnPressedTime[n]);
          xQueueSend(control_evt_queue, (void *) &evt, 10);
        }
      }
    }
    vTaskDelay(BTN_POLL_PERIOD / portTICK_PERIOD_MS);
  }
}

// INIT HW
void init_hw() {

  // Button GPIO Init
  gpio_config_t config = {};
  config.mode = GPIO_MODE_INPUT;
  config.pull_up_en = GPIO_PULLUP_ENABLE;
  config.pull_down_en = GPIO_PULLDOWN_DISABLE;
  config.intr_type = GPIO_INTR_DISABLE;
  config.pin_bit_mask = 1LL << GPIO_BTN1;
  gpio_config(&config);
  config.pin_bit_mask = 1LL << GPIO_BTN2;
  gpio_config(&config);
  config.pin_bit_mask = 1LL << GPIO_INTERNAL_BUTTON;
  gpio_config(&config);
}


esp_err_t init_spiffs() {
  esp_vfs_spiffs_conf_t conf = {
    .base_path = "/spiffs",
    .partition_label = NULL,
    .max_files = 5,
    .format_if_mount_failed = false,
  };

  esp_err_t ret = esp_vfs_spiffs_register(&conf);
  if (ret == ESP_OK) {
    size_t total = 0, used = 0;
    ret = esp_spiffs_info(conf.partition_label, &total, &used);
    if (ret == ESP_OK) {
      ESP_LOGI(TAG, "SPIFFS initialized. Partition size: total: %d, used: %d", total, used);
    } 
  } else {
    ESP_LOGI(TAG, "SPIFFS error %d", ret);
  }
  return ret;
}

void app_main() {
  esp_err_t ret;

  // HW Init
  init_hw();

  // Control
  ESP_LOGI(TAG, "----Init CONTROL...");
  control_init(GPIO_RELAY_LAST, GPIO_RELAY_NEXT, GPIO_LED_GREEN, GPIO_LED_RED);
  control_evt_queue = control_get_queue();

  //Initialize NVS
  ret = nvs_flash_init();
  if (ret == ESP_ERR_NVS_NO_FREE_PAGES || ret == ESP_ERR_NVS_NEW_VERSION_FOUND) {
    ESP_ERROR_CHECK(nvs_flash_erase());
    ret = nvs_flash_init();
  }
  ESP_ERROR_CHECK(ret);

  // File System Init
  ESP_LOGI(TAG, "----Init SPIFFS...");
  init_spiffs();
  
  // CONFIG
  ESP_LOGI(TAG, "----Init CONFIG...");
  ret = config_init();
  if ( ret == ESP_OK) {
    // Cable & IR release
    uint8_t code = config_get_ir_selected_code();
    code = code > 0 ? code - 1 : 0;
    uint8_t divider = config_get_ir_divider(code);
    uint32_t freq = config_get_ir_freq(code);
    ir_release_init(GPIO_IR_RELEASE, RMT_CHANNEL_0, divider, freq);
    cable_release_init(GPIO_CABLE_RELEASE_SHUTTER, GPIO_CABLE_RELEASE_FOCUS);
    control_set_cable_release_queue();

    // Task button
    ESP_LOGI(TAG, "----Init TASK button...");
    xTaskCreate(&task_button, "task_button", 2048, NULL, 10, NULL);

    // WiFi
    ESP_LOGI(TAG, "----Init WiFi...");
    wifi_init();
    wifi_init_ap_sta();

    // http Server 
    server_init();
  } else {
    // Init Error
    control_evt_t evt;
    ESP_LOGE(TAG, "CONFIG ERROR err no = %d", ret);
    evt = CONTROL_EVT_ERROR; 
    xQueueSend(control_evt_queue, (void *) &evt, 10);
  }
}

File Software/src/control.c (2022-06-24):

#include <string.h>
#include <stdio.h>
#include "freertos/FreeRTOS.h"
#include "freertos/task.h"
#include "freertos/queue.h"
#include "esp_log.h"
#include "esp_timer.h"
#include "esp_wifi.h"
#include "project.h"
#include "config.h"
#include "server.h"
#include "wifi.h"
#include "control.h"

// Local Types
typedef enum {
  LED_STATE_OFF,
  LED_STATE_ON,
  LED_STATE_BLINK,
  LED_STATE_BLINK_SLOW,
} led_states_t;

// LOG TAG
static const char *TAG = "control";

// Local variables
static QueueHandle_t control_evt_queue = NULL;
static QueueHandle_t cable_release_evt_queue = NULL;
static control_states_t _current_state;
static bool autoScan = false;
static uint8_t current_slide = 0;
static gpio_num_t pin_last = 0;
static gpio_num_t pin_next = 0;
static gpio_num_t pin_led_gn = 0;
static gpio_num_t pin_led_rd = 0;
static esp_timer_handle_t delay_timer;
static esp_timer_handle_t pulse_timer;

// Local functions
static void state_idle_entry(void);
static void state_error_entry(void);
static void state_next_entry(void);
static void state_last_entry(void);
static void state_scan_entry(void);
static void control_start_delay_timer(uint32_t delay_ms);
static void control_stop_delay_timer();
static void control_start_pulse_timer(uint32_t delay_ms);
static void control_stop_pulse_timer();
static void control_update_current_slide(uint8_t val);
static void control_update_auto_scan_button();


// Timer Handler
static void delay_timer_callback(void* arg)
{
  ESP_LOGI(TAG, "delay_timer Handler");

  control_evt_t evt = CONTROL_EVT_TIMER;
  xQueueSend(control_evt_queue, (void *) &evt, 10);
}

static void pulse_timer_callback(void* arg)
{
  ESP_LOGI(TAG, "pulse_timer Handler");

  gpio_set_level(pin_last, 0);
  gpio_set_level(pin_next, 0);

  if (!autoScan) {
    control_evt_t evt = CONTROL_EVT_TIMER;
    xQueueSend(control_evt_queue, (void *) &evt, 10);
  }
}


// --------------------------------------------------------------------------------------------------
// State: IDLE
// --------------------------------------------------------------------------------------------------
static void state_idle_entry(void) {
  ESP_LOGI(TAG, "entry: CONTROL_STATE_IDLE");
  _current_state = CONTROL_STATE_IDLE;
  gpio_set_level(pin_last, 0);
  gpio_set_level(pin_next, 0);
  control_stop_delay_timer();
  control_stop_pulse_timer();
  autoScan = false;
}

static void state_idle(control_evt_t argEvt) {
  switch (argEvt) {
    case CONTROL_EVT_NONE:
      break;

    case CONTROL_EVT_NEXT:
      autoScan = false;
      state_next_entry();
      break;

    case CONTROL_EVT_LAST:
      autoScan = false;
      state_last_entry();
      break;

    case CONTROL_EVT_START:
      autoScan = true; 
      state_next_entry();
      break;

    case CONTROL_EVT_STOP:
      break;

    case CONTROL_EVT_SCAN:
      autoScan = false;
      state_scan_entry();
      break;

    case CONTROL_EVT_TIMER:
      break;

    case CONTROL_EVT_RESET_CURRENT_SLIDES:
      control_update_current_slide(0);
      break;

    case CONTROL_EVT_ERROR:
      state_error_entry();
      break;

    default:
      state_idle_entry();   // Should not happen, stay in IDLE state
      break;
  }
}


// --------------------------------------------------------------------------------------------------
// State: ERROR
// --------------------------------------------------------------------------------------------------
static void state_error_entry(void) {
  ESP_LOGI(TAG, "entry: CONTROL_STATE_ERROR");
  _current_state = CONTROL_STATE_ERROR;
}

static void state_error(control_evt_t argEvt) {
  switch (argEvt) {
    case CONTROL_EVT_NONE:
      break;

    case CONTROL_EVT_NEXT:
      break;

    case CONTROL_EVT_LAST:
      break;

    case CONTROL_EVT_START:
      break;

    case CONTROL_EVT_STOP:
      break;

    case CONTROL_EVT_SCAN:
      break;

    case CONTROL_EVT_TIMER:
      break;

    case CONTROL_EVT_ERROR:
      state_error_entry();
      break;

    default:
      state_idle_entry();   // Should not happen, stay in IDLE state
      break;
  }
}


// --------------------------------------------------------------------------------------------------
// State: CONTROL_STATE_NEXT
// --------------------------------------------------------------------------------------------------
static void state_next_entry(void) {
  ESP_LOGI(TAG, "entry: CONTROL_STATE_NEXT");
  if (current_slide < config_get_slides_to_scan()) {
    control_update_current_slide(current_slide + 1);    
    _current_state = CONTROL_STATE_NEXT;
    gpio_set_level(pin_next, 1);
    control_start_delay_timer(config_get_delay_slide_change());
    control_start_pulse_timer(config_get_time_slide_change_pulse());
  }
  else {
    // all slides are scanned, nothing to do
    state_idle_entry();
  }
}

static void state_next(control_evt_t argEvt) {
  switch (argEvt) {
    case CONTROL_EVT_NONE:
      break;

    case CONTROL_EVT_NEXT:
      break;

    case CONTROL_EVT_LAST:
      break;

    case CONTROL_EVT_START:
      break;

    case CONTROL_EVT_STOP:
      state_idle_entry();
      break;

    case CONTROL_EVT_SCAN:
      break;

    case CONTROL_EVT_TIMER:
      autoScan ? state_scan_entry() : state_idle_entry();
      break;

    case CONTROL_EVT_ERROR:
      state_error_entry();
      break;

    default:
      state_idle_entry();   // Should not happen, go to IDLE state
      break;
  }
}


// --------------------------------------------------------------------------------------------------
// State: CONTROL_STATE_LAST
// --------------------------------------------------------------------------------------------------
static void state_last_entry(void) {
  ESP_LOGI(TAG, "entry: CONTROL_STATE_LAST");
  if (current_slide > 0) {
    control_update_current_slide(current_slide - 1);
    _current_state = CONTROL_STATE_LAST;
    gpio_set_level(pin_last, 1);
    control_start_delay_timer(config_get_delay_slide_change());
    control_start_pulse_timer(config_get_time_slide_change_pulse());  
  }
  else {
    // First slide reached, nothing to scan
    state_idle_entry();
  }
}

static void state_last(control_evt_t argEvt) {
  switch (argEvt) {
    case CONTROL_EVT_NONE:
      break;

    case CONTROL_EVT_NEXT:
      break;

    case CONTROL_EVT_LAST:
      break;

    case CONTROL_EVT_START:
      break;

    case CONTROL_EVT_STOP:
      state_idle_entry();
      break;

    case CONTROL_EVT_SCAN:
      break;

    case CONTROL_EVT_TIMER:
      state_idle_entry();
      break;

    case CONTROL_EVT_ERROR:
      state_error_entry();
      break;

    default:
      state_idle_entry();   // Should not happen, go to IDLE state
      break;
  }
}
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
